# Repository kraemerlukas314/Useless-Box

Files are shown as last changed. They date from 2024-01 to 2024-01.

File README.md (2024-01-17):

# Useless-Box
Useless box project of Melvin Göttsche, Lukas Krämer and Mario Stötzel, Smart Technology Students at FH Wedel.  

This project was chosen as a freshmans project to learn about electronics, programming as well as basic manufacturing techniques such as laser cutting and 3d printing. More information about this project can be found in the [docs](https://github.com/kraemerlukas314/Useless-Box/tree/main/docs) folder of this repo (all in german).
If you want to build this project yourself, please check out the needed parts in the developer documentation.    
Image of our useless box

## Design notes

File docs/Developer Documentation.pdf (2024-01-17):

# Entwicklerdokumentation

# Useless Box mit Emotionen

## WS23/24, Smart Technology

## Melvin Göttsche, Lukas Krämer, Mario Stötzel

## Einführung

Als Erstsemesterprojekt haben wir uns dazu entschieden eine sogenannte Useless Box zu bauen. Diese besteht im Wesentlichen aus einem Schalter, der nach Umlegen durch den Nutzer mithilfe eines Servo Motors wieder in seine Ausgangsposition gebracht wird.

Die Useless Box ist zwar wenig sinnvoll, allerdings bietet sie sich insbesondere als erstes Projekt an, da sie
sowohl | elektronische | als | auch | mechanische | und | softwareseitige | Aspekte | beinhaltet.
Dieses Dokument soll einen guten Überblick über die Hardware sowie Software der Box vermitteln und dabei helfen, das Projekt gegebenenfalls nachzubauen, zu erweitern oder reparieren zu können.

## Überblick Hardware

Die Hardware der Useless-Box wurde auf Grundlage der verschiedenen Eigenschaften, die zu Beginn des Projektes für die Box ausgewählt wurden, festgelegt. Bei den Materialien haben wir uns für einfache Leimholzplatten entschieden. Diese Leimholzplatten haben eine Stärke von 4mm, was trotz des geringen Gewichtes die Stabilität, aber auch die Mobilität und Einfachheit der Useless-Box aufrechterhält. Die Box hat die Außenmaße von 22 x 12 x 12 cm (L/H/B), ist einfach zusammengesetzt und besteht aus einer Kiste mit einem zweigeteilten Deckel.

Wir haben eine besonders Eigenschaft hinzugefügt, mit der die Box mit Hilfe eines Displays Emotionen in Form von digitalen Gesichtern anzeigen kann. Um dieses umzusetzen, besitzt die eine Hälfte des Deckels der Useless-Box eine Vertiefung, die mit einer durchsichtigen Plexiglasscheibe abgedeckt wird, um das darunter befindlichen Displays zu schützen. Außerdem wurde auf dieser Seite der Box ein zusätzliches Loch ausgeschnitten, um einen Kippschalter für die Hauptfunktion der Box unterzubringen. Die andere Hälfte des Deckels ist einfach gestaltet und hat nur die Funktion einer Klappe.

In der Box selbst wurden für den Hauptmechanismus eine Halterung für einen Servo-Motor sowie mit der Grundplatte verleimte Standfüße zur Befestigung der Platine montiert.

Wesentliche Teile des Gehäuses, welche die Wände, den Boden, die Standfüße der Platine und Teile der Halterung für den Servo-Motor beinhalten, wurden als dauerhafte Verbindungen mit Leim befestigt. Andere Teile jedoch wie der Motor und die Platine wurden verschraubt, um eine Wartung zu ermöglichen. Die Plexiglasabdeckung wurde mit Silikon befestigt, um die Anzeige des Displays nicht zu beeinträchtigen. Die Klappe im Deckel wurde mit Scharnieren montiert.

Der Arm des Servo-Motors der Useless-Box ist das einzige Teil, welches aus Plastik in einem 3D-Drucker hergestellt wurde. Die Holzelemente und Plexiglaselemente wurden gelasert und nur einzelne Teile zusätzlich gebohrt. Alle Holzkomponenten wurden außerdem grundiert, geschliffen und dann in schwarz lackiert.

Zur Vorbereitung der Projektumsetzung haben wir zudem mit Hilfe einer Software und in Pappe ein 3D Model des Grundprinzips der Box entworfen, an welchem später noch Optimierungen bis zum finalen Produkt gefunden werden konnten.

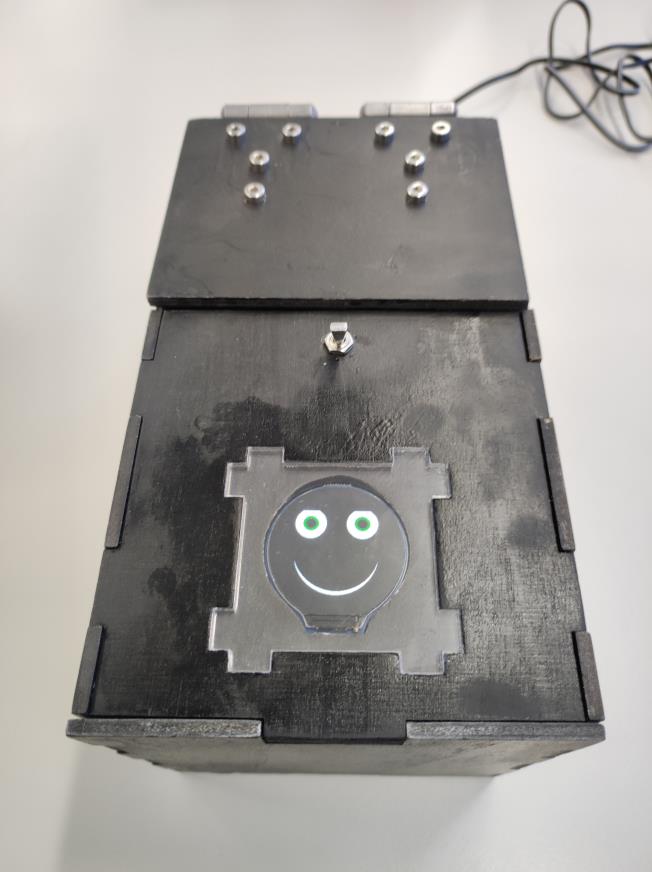
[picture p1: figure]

Bild 1: fertige Box

## Überblick Elektronik

Die Elektronik unserer Useless Box sollte in der Lage sein, einen Servo anzusteuern (für das Umlegen des Arms), einen Schalter auszulesen und dem Benutzer in Form eines Displays Feedback geben zu können. Angeboten hat sich daher die Nutzung eines Arduino Nano Mikrocontrollers, da er nicht nur unsere Anforderungen erfüllt, sondern wir durch private Projekte auch schon Erfahrung mit dem Board gesammelt haben und so die Entwicklung beschleunigt werden konnte.

Neben einem gewöhnlichen Schalter zum Umlegen, verwenden wir noch einen HiTec Servo, der den Arm bewegt, um später den Schalter umlegen zu können. Außerdem haben wir uns für ein rundes Display entschieden, was sich für das Darstellen von einem digitalen Gesicht als günstig erwies. Damit die Elektronik zuverlässig funktioniert und die Entwicklung nicht durch schwer reproduzierbare Wackelkontakte erschwert wird, haben wir uns von Anfang an dazu entschieden, für die gesamte Elektronik eine Leiterplatte zu erstellen.

Diese wurde zunächst in EasyEDA (Bild 2 und 3) designt und anschließend gefräst (Bild 4). Nach der Bestückung und kurzem Rauchtest haben wir nacheinander die Komponenten eingebaut und die Subsysteme der Reihe nach getestet.

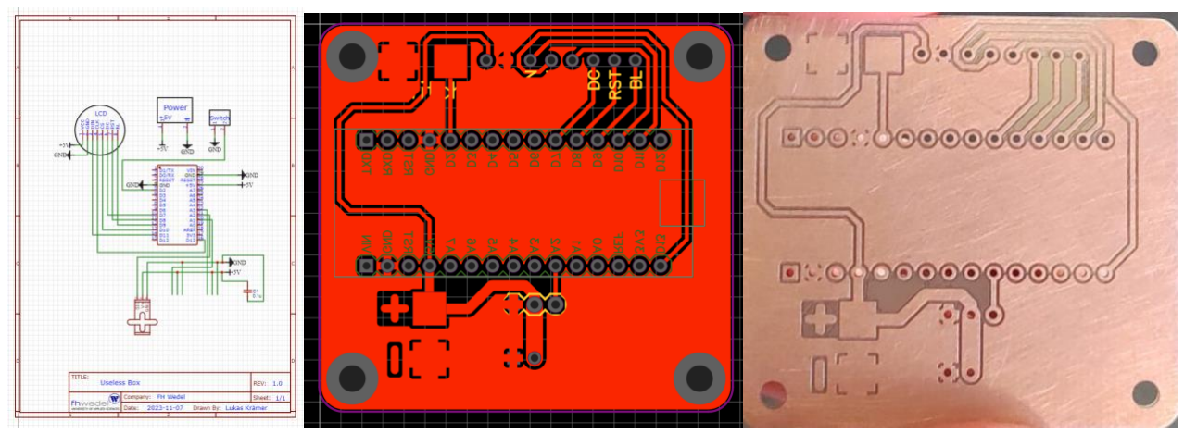
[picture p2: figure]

Bild 2: Schaltplan | Bild 3: Platine | Bild 4: gefräste Platine

## Überblick Software

Die Box fängt damit an den Zähler auf dem Display anzuzeigen, wie oft der Schalter bereits umgelegt worden ist. Sie zeigt diese Zahl so lange an, bis der Schalter umgelegt wird. Hiernach wird der Arm ausgefahren, bis der Schalter umgelegt wurde. Dies wird genutzt, um die Position des Schalters intern zu speichern. Damit sich die Box “merken” kann, wie oft der Schalter bereits umgelegt wurde, schreiben wir einen Zähler (unsigned, vier bytes groß) nach jedem Umlegen in die EEPROM des Arduinos. Da eine einzelne EEPROM Speicherzellen lediglich 100.000-mal beschrieben werden kann (100.000 stehen als “garantiert” im Datenblatt, unabhängige Tests ergaben deutlich höhere Zahlen) und wir dafür sorgen möchten, dass unsere Box auch so lange wie möglich korrekt funktioniert, haben wir uns dazu entschieden, ein rollierendes System zu verwenden, was im Folgenden näher erläutert wird. Das Abspeichern in die EEPROM erfolgt byteweise, also könnte man in Adresse 0 das LSB schreiben und die anderen drei Bytes in Adressen 1, 2 und 3. Da das aber nach 100.000 Schreibzyklen nicht mehr garantiert funktionieren würde, werden Byte 1, 2 und 3 in die Adressen 16, 17 und 18 geschrieben. Das LSB, was sich am häufigsten ändert, wird hingegen in einer Adresse zwischen 0 und 15 abgespeichert. Wird der Code initial auf dem Arduino ausgeführt, befindet sich in den Adressen 0 bis 15 überall eine 0, der Arduino wählt nun per “Zufallsgenerator” (millis mod 16) eine der Adressen aus und schreibt dort eine
1. Beim nächsten Schalterumlegen sucht er jetzt in den Adressen zwischen 0 und 15 die Adresse, deren Wert größer als 0 ist, folglich wird wieder in dieselbe Adresse wie zuvor geschrieben, bis der Wert 256 bzw. 0 erreicht wird. Dort wird dann erneut eine zufällige Adresse ausgewählt, um das LSB des Zählers abzuspeichern, die sich sehr wahrscheinlich (93,75%) von der letzten Adresse unterscheidet. Dadurch verschleißt die EEPROM deutlich langsamer und kann zumindest Zähler bis 1,6 Millionen garantiert abspeichern. Natürlich kann dieses System beliebig erweitert werden, sodass beispielsweise die ersten 32 oder 64 Adressen fürs Rollieren genutzt werden, was die Langlebigkeit weiter steigern würde.

Die Hauptmethode der Useless Box ist der Loop des Arduinos. Dieser wurde mit einer while Schleife getaktet, um die Animationen besser vorherzusehen. Sollte der Schalter in der Off-Position stehen, wird eine Variable happiness bis zu einem bestimmten Wert erhöht. Sollte der Schalter umgelegt worden sein und es läuft noch keine Animation, wird eine Animation zufällig ausgewählt, der Zähler für die Gesamtzahl der Schalterumlege erhöht und die happiness um einen Wert reduziert. Sollte der Schalter vom Nutzer wieder zurückgelegt worden sein, während eine Animation noch läuft, so wird die Animation abgebrochen und der Arm zurückgefahren. Sollte eine Animation noch laufen, so wird eine Funktion aufgerufen, die wiederum die Funktion für die Animation direkt aufruft. Die Animationen werden in Steps aufgeteilt, damit die Main “zeitgleich” nebenbei laufen kann. Der erste Step jeder Animation ist es, den Servo zu attachen. In jedem Step wird, nachdem der Step abgeschlossen ist ein Zähler erhöht, welcher repräsentiert, welcher Step gerade dran ist. Um den Arm zu bewegen kann eine Funktion verwendet werden, der man sagen kann, wo der Arm hinsoll und in wie vielen Schritten er dort ankommen soll. Hierfür bestimmt die Funktion beim ersten Aufruf wie weit sich der Arm bei jedem Aufruf bewegen soll und gibt true zurück, wenn die finale Position erreicht worden ist.

Sollte im Moment keine Animation aktiv sein, wird das Gesicht auf dem Display aktualisiert. Hierbei wird die Variable happiness betrachtet und das Gesicht wird dementsprechend glücklich oder unglücklich gezeichnet. Bei jedem x-ten Aufruf der Hauptfunktion wird außerdem eine Funktion aufgerufen, die die Box blinzeln lässt, um sie humaner rüberkommen zu lassen.

## Was wir nächstes Mal besser machen würden

Für unser nächstes Projekt sollten wir von Anfang an den Aspekt der einfachen Wart- und Reparierbarkeit denken, da bei uns aktuell viele Teile dauerhaft fest geleimt oder nur schwer erreichbar sind. Mit genug Zeit lässt sich zwar jedes Teil tauschen, allerdings ist dies teils mit hohem Aufwand verbunden.

## Wartungstätigkeiten

Zwar ist es schwierig, nach lediglich so kurzer Nutzung potentielle “Point of Failures” aufzuführen, wahrscheinlich wird jedoch als Erstes unser einziges bewegliches Teil, der Servo, versagen. Dieser kann getauscht werden, indem man zunächst die “Serviceklappe” hochhebt, die Servohalterung abschraubt und anschließend den Servo selbst aus seiner Halterung entfernt. Nach Einsetzen des neuen Servos, sollte die finale Servoposition anhand der beiden großen Schrauben, welche die Servohalterung mit der Box verbinden adjustiert werden, damit die Hand den Schalter der Box korrekt umlegen kann.

## Weiterentwicklung

Was die Weiterentwicklung des Projektes betrifft, haben wir über das Ergänzen von RGB Leds nachgedacht, die zusätzlich zum Display die Emotionen der Box darstellen können. Diese könnte entweder von außen an die Box angebracht werden oder aber in Form von RGB-Streifen von innen in die Box geklebt werden, sodass sie durch die Klappe der Box scheinen, sobald der Servo diese hochhebt. Außerdem könnte eine SD-Karte mit verschiedenen Soundeffekten samt kleinem Lautsprecher ergänzt werden, um die Nutzung der Box noch interessanter zu gestalten. Abgespielt werden können dabei zum Beispiel Soundeffekte beim Umlegen des Schalters (bspw.: stöhnen, wenn die Box genervt ist). Zu guter Letzt können die von uns erstellen Animationen softwareseitig natürlich beliebig erweitert oder abgeändert werden, was die Nutzung der Box sicherlich interessanter machen würde. Die Weiterentwicklung des Codes darf natürlich gerne in Form einer Pull-Request in unser Repository ergänzt werden.

## Einrichten der Entwicklungsumgebung

Um an der Box weiterarbeiten zu können, muss zunächst die Arduino IDE (https://www.arduino.cc/en/software) heruntergeladen und installiert werden. Außerdem werden noch die beiden Libraries “Adafruit_GFX” (https://github.com/adafruit/Adafruit-GFX-Library) und “Adafruit_GC9A01A” (https://github.com/adafruit/Adafruit_GC9A01A) benötigt. Damit das Abspeichern des Schalterzählers in die EEPROM wie erwartet funktioniert, sollten außerdem die ersten 19 Adressen (also 0 bis 18) mit einer 0 beschrieben werden, dies erfolgt über den Befehl EEPROM.write(Adresse, 0). (https://docs.arduino.cc/learn/built-in-libraries/eeprom)

Der gesamter Sourcecode samt weiter Informationen ist in unserem GitHub Repository (https://github.com/kraemerlukas314/Useless-Box/) zu finden.

## Teileliste

- Arduino Nano (https://store.arduino.cc/products/arduino-nano)
- Waveshare 1.28inch Round LCD Module Display (https://www.amazon.de/dp/B08V5538C6)
- Servo HS-645MG (https://www.servonaut.de/shop/en/product_info.php?info=p460_servo-hs-645mg.html)
- 5V Netzteil (2.5A) (https://www.conrad.de/de/p/voltcraft-vc-11332635-steckernetzteil-festspannung-5-v-dc-2-5-a-12-5-w-2266527.html)
- Buchse zum Netzteil (https://www.conrad.de/de/p/tru-components-niedervolt-steckverbinder-buchse-einbau-vertikal-5-5-mm-2-5-mm-1-st-1564887.html)
- Schalter (https://www.conrad.de/de/p/tru-components-1587776-tc-ta101f1-kippschalter-250-v-ac-3-a-1-x-aus-ein-rastend-1-st-1587776.html)
- 2x Scharnier 35mm*125mm*1,5mm mit M4 Löchern
- 100 µF Elektrolyt-Kondensator (https://www.conrad.de/de/p/teapo-sy-100-f-16v-6-3-x11mm-elektrolyt-kondensator-radial-bedrahtet-2-5-mm-100-f-16-v-20-o-x-l-6-3-mm-x-11-mm-1-443906.html)
- 8x Senkkopfschraube M4 10mm (https://www.conrad.de/de/p/toolcraft-888802-senkkopfschrauben-m3-20-mm-t-profil-mit-stift-edelstahl-a2-10-st-888802.html)
- 8x Schraube M4 14mm
- 16x Mutter M4
- 8x Schraube M3 10mm
- 8x Mutter M3
- 2x Unterlegscheibe M5
- 2x Unterlegscheibe M6
- 2x Schraube M5 45mm
- 1420cm²
Leimholzplatten, 4mm dick (ohne Bohrungen)
- Holzblock 72 cm²
- 1m 0.75mm² Kupferkabel
- Holzleim
- Spraydose Grundierung
- Spraydose Scharz (Matt)
- 28cm² Plexiglas
- Silikon
- 2x Schraubenniete M5

## Werkzeug

- Mini USB Kabel, zum Hochladen von Code auf den Arduino
- Lötkolben
- Lötzinn
- Abisolierzange
- Entsprechende Schraubendreher
- Schraubzwingen, um geleimte Teile zu fixieren
- Lasercutter
- 3D Drucker
- Kartuschenpresse
- Schleifpapier
- Feilen
- Nietenzange

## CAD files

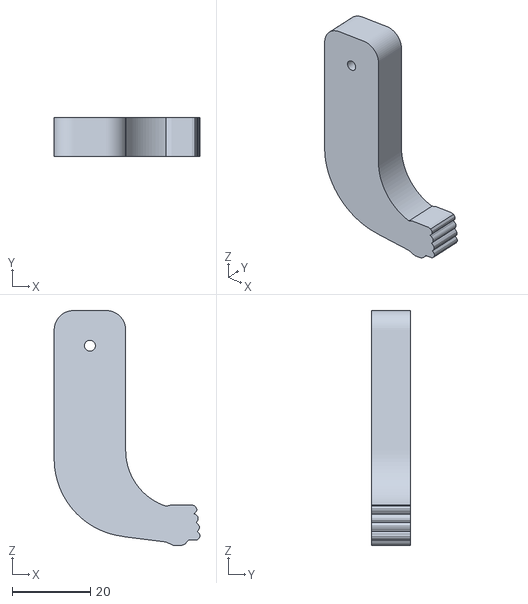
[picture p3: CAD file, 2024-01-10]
files/Hardware/arm.stl
37.3 x 10.0 x 60.2

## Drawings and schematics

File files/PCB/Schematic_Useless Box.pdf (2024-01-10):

## LCD

+5V -

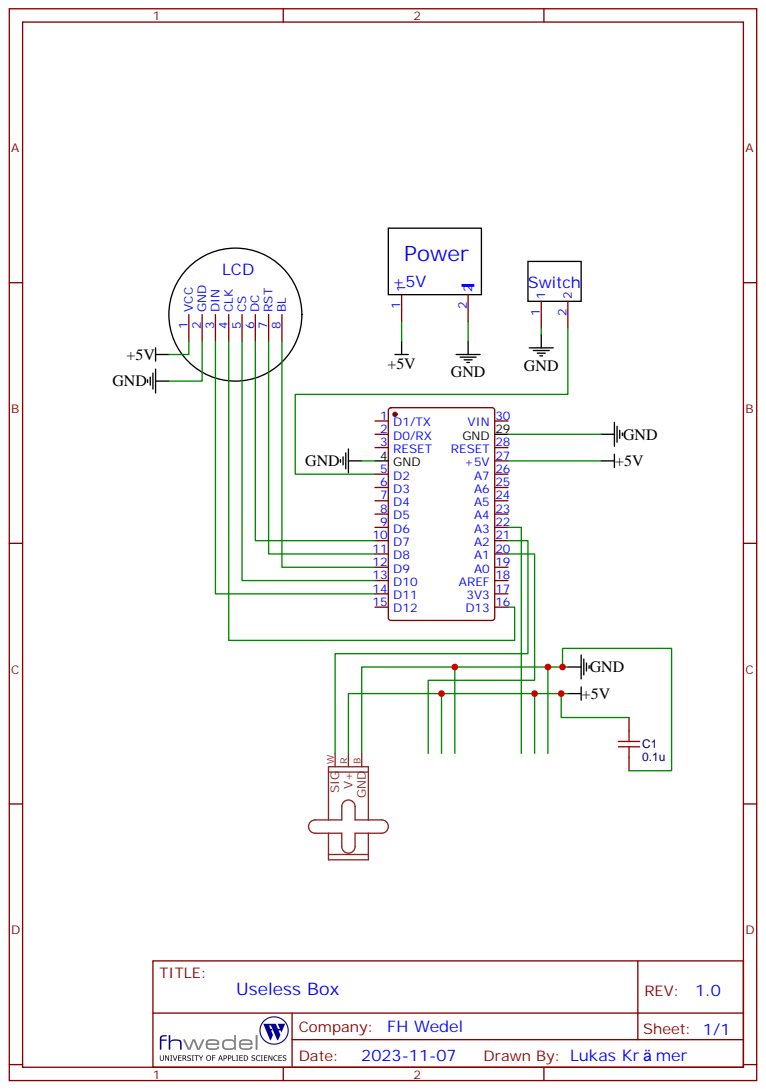
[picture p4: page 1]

Drawn By: Lukas Kr mer

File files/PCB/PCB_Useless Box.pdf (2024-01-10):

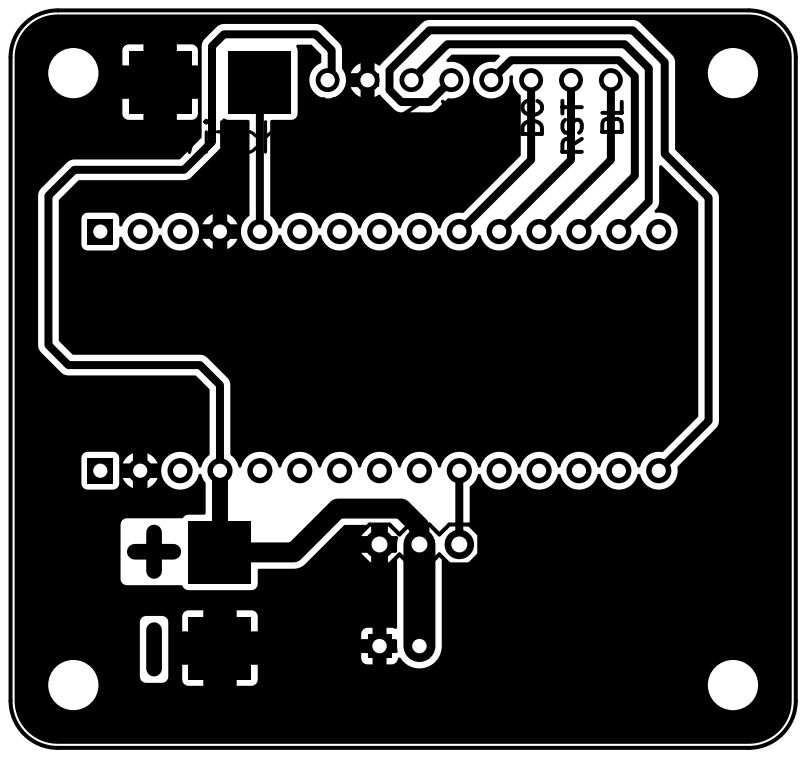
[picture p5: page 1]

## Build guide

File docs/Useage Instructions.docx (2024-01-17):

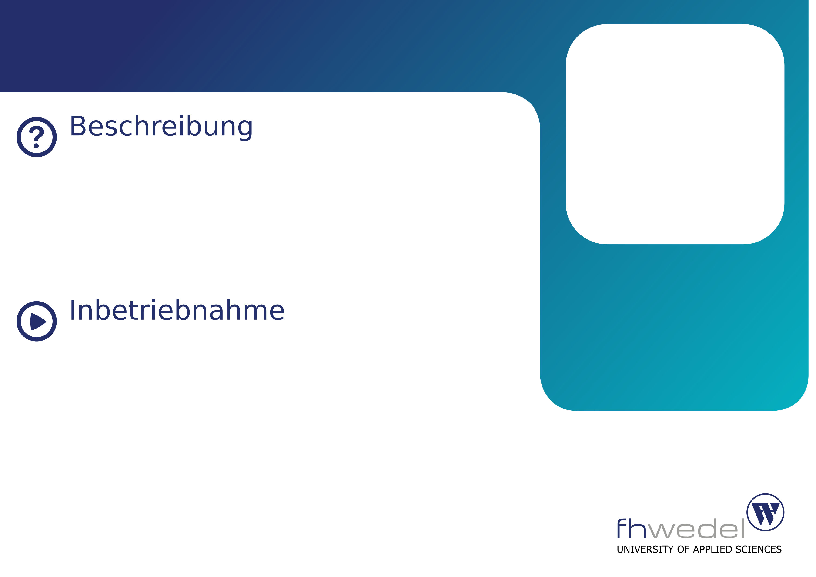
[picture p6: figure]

Useless Box

Diese Useless Box ist als Erstsemesterprojekt entstanden, dessen Ziel es war, möglichst viele Maschinen zu nutzen, um die Box zu fertigen und Erfahrung für den späteren Studienverlauf zu sammeln. So kamen unter anderem ein Laser Cutter (Gehäuse), ein 3D Drucker (Arm) und eine Fräse (Platine) zum Einsatz.

1. Semester | WS23

Lukas Krämer

Mario Stötzel

Melvin Finn Göttsche

Zum Einschalten der Box muss lediglich das Netzteil eingesteckt werden. Anschließend kann der Schalter „nach oben“ umgelegt werden, der dann automatisch zurück in die Ausgangsposition gebracht wird.

Nach dem Umlegen des Schalters sollte stets darauf gewartet werden, dass er von der Maschine zurückgelegt wird, also bitte nicht manuell den Schalter fünf mal hin und her schalten.

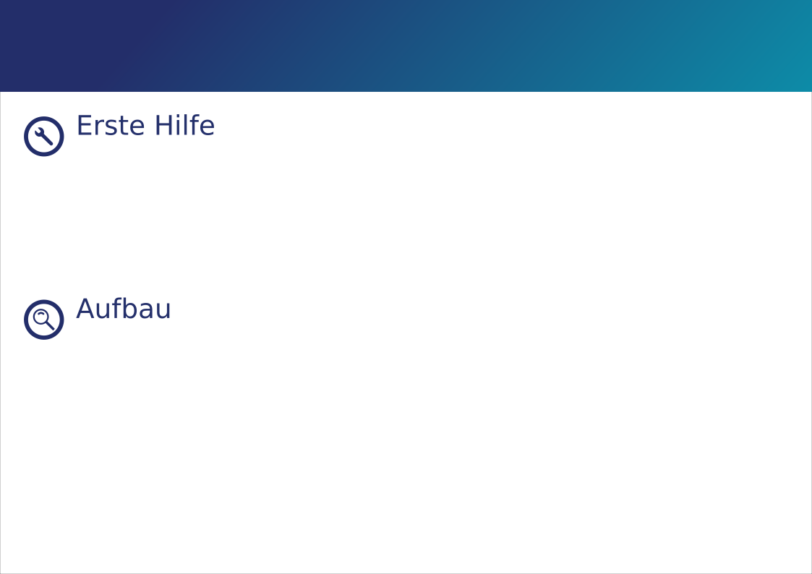
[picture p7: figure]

Die Überschrift

Q: Die Box ignoriert mich

A: Bitte lege den Schalter um

In allen anderen Fällen: „Have you tried turning it off and on again?“

Falls auch das nicht hilft, ist vermutlich ein Kabel im Inneren der Box abgerissen. Bitte wende dich an ein Mitglied der FH Wedel.

Das Herzstück unserer Useless Box bildet ein Mikrocontroller, an den ein Servomotor, das zu sehende Display sowie der Schalter angeschlossen sind.

Sobald der Schalter umgelegt wird, steuert der Mikrocontroller den Servomotor an, um ihn wieder in seinen Ausgangszustand zu bewegen. Außerdem wird darauf basierend die Emotionslage angepasst.

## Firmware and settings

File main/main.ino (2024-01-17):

#include "defines.h"

Adafruit_GC9A01A tft(TFT_CS, TFT_DC);

Servo servo;

int eyesColor = 0x0066ff;
int eyesColorSize = EYES_SIZE / 2;
int eyesPupilSize = EYES_SIZE / 2.8;
long timeLast = millis();
int happiness = random(100);
int blinker = 0;
int blinkTimer = 200;
byte servoPosSwitch = 0;
byte servoPosHome = 0;
byte servoPosCurrent = 0;
byte SERVO_TOGGLE_POS; // is a variable but is only changed once
byte SERVO_HOME_POS;
const byte SERVO_DELTA_TOOGLE_HOME = 120; // difference between toogle pos and home pos
int activeAnimation = -1;
int eyeLeftActualPositionX = 0;
int eyeLeftActualPositionY = 0;
int eyeRightActualPositionX = 0;
int eyeRightActualPositionY = 0;
int eyeLidActualPositionLL = 0;
int eyeLidActualPositionLR = 0;
int eyeLidActualPositionRL = 0;
int eyeLidActualPositionRR = 0;
int mouthActualStatus = -100000;
int eyesActualColor = 0;
bool buttonPushedByArm = true;
int animationStep = 0;
bool animationFinished = true;
bool armAnimationInited = false;
int armAnimationDeg = 0;
bool sleeping = false;
int tiredness = 0;
int sleepTimer = 200;
int maxSleepZs = 3;
int sleepZCounter = maxSleepZs;

void setup()
{
  randomSeed(analogRead(0));
  Serial.begin(115200);
  Serial.println("---- NEW START ----");
  tft.begin();
  pinMode(PIN_BTN, INPUT_PULLUP);
  servo.attach(PIN_SERVO);
  servo.write(180);
  servo.detach();
  displayClear();

  // if counter is < 999999 -> fill empty digits with zeros so string always has length 6
  String formattedString = String(getButtonPresses());
  while (formattedString.length() < 6)
  {
    formattedString = "0" + formattedString;
  }
  tft.setTextSize(6);
  tft.setCursor(16, 95);
  tft.print(formattedString);

  // wait for user to toggle button
  while (!getButtonState())
  {
  }
  servo.attach(PIN_SERVO);
  // Calibrate servo position
  servoPosCurrent = servo.read();
  while (getButtonState() && servoPosCurrent > 0)
  {
    servoPosCurrent = servoPosCurrent - 1;
    servo.write(servoPosCurrent);
    delay(15);
  }
  SERVO_TOGGLE_POS = servoPosCurrent + 7;
  SERVO_HOME_POS = 180; // SERVO_TOGGLE_POS + SERVO_DELTA_TOOGLE_HOME;
  servo.write(SERVO_HOME_POS);
  Serial.println("SERVO_HOME_POS: " + String(SERVO_HOME_POS));
  Serial.println("SERVO_TOGGLE_POS: " + String(SERVO_TOGGLE_POS));
  displayClear();
  eyesRedraw();
  eyeLidsRedraw();
  mouthDrawStatus(0);
  servo.detach();
}

void loop()
{
  while (millis() - timeLast < intervall)
  {
  }
  timeLast = millis();

  if (!getButtonState() && activeAnimation == -1)
  {
    if (happiness < MAX_HAPPINESS)
    {
      happiness += happinessAdder;
    }

    if (tiredness < SLEEP_TIME)
    {
      tiredness++;
    }
    if (!sleeping)
    {
      handleStandardExpression();
    }
  }
  else if (!getButtonState() && activeAnimation != -1 && !buttonPushedByArm)
  {
    Serial.println("Button pressed while playing animation. Cancelling animation...");
    armAnimationInited = false;
    resetAnimation();
    activeAnimation = -1;
    animationStep = 0;
    if (happiness + happinessAdder * 10 <= MAX_HAPPINESS)
    {
      happiness += happinessAdder * 10;
    }
  }
  else if (getButtonState() && activeAnimation == -1)
  {
    if (happiness - dissatisfaction >= MIN_HAPPINESS)
    {
      happiness -= dissatisfaction;
    }
    activeAnimation = random(1, maxArmAnimations + 1);
    animationStep = 0;
    buttonPushedByArm = false;
    incrementButtonPresses();
    if (tiredness - 3000 > 0)
    {
      tiredness -= 3000;
    }
    else
    {
      tiredness = 0;
    }
    sleeping = false;

    Serial.println("Starting new animation: " + String(activeAnimation));
  }

  if (activeAnimation != -1)
  {
    handleStandardExpression();
    handleButtonPressed();
    blinker = blinker / 2;
  }

  // Blinking
  if (blinker <= 0 && !sleeping)
  {
    eyesBlink();
    blinker = blinkTimer;
  }
  else
  {
    --blinker;
  }
  if (sleeping)
  {

    if (sleepTimer <= 0)
    {
      if (sleepZCounter >= maxSleepZs)
      {
        displayClear();
        sleepZCounter = 0;
      }
      tft.setTextSize(random(3, 7));
      tft.setCursor(random(25, 215), random(25, 215));
      tft.print('z');
      sleepZCounter++;
      sleepTimer = 200;
    }
    else
    {
      sleepTimer--;
    }
  }
}

bool getButtonState()
{
  static int lastButtonState = HIGH, buttonState;
  static unsigned long lastDebounceTime;

  buttonState = digitalRead(PIN_BTN);
  if (buttonState != lastButtonState)
    lastDebounceTime = millis();

  return !((millis() - lastDebounceTime) > 50 ? lastButtonState = buttonState : !lastButtonState);
}

// increments the total button counter and writes result to EEPROM
void incrementButtonPresses()
{
  EEPROMWritelong(getButtonPresses() + 1);
}

uint32_t getButtonPresses()
{
  // TODO: read from eeprom:
  byte one = 0;
  for (int i = 0; i < 16; ++i)
  {
    if (EEPROM.read(i) > 0)
      one = EEPROM.read(i);
  }
  byte two = EEPROM.read(16);
  byte three = EEPROM.read(17);
  byte four = EEPROM.read(18);
  return (uint32_t)four << 24 | (uint32_t)three << 16 | (uint32_t)two << 8 | (uint32_t)one;
}

void EEPROMWritelong(long value)
{
  byte one = (value & 0xFF);
  byte two = ((value >> 8) & 0xFF);
  byte three = ((value >> 16) & 0xFF);
  byte four = ((value >> 24) & 0xFF);

  // to avoid eeprom wear down, least significant byte (that changes very frequently)
  // is written somewhere between address 0 and 15
  byte address_to_write = 0;
  for (int i = 0; i < 16; ++i)
  {
    if (EEPROM.read(i) > 0)
      address_to_write = i;
  }
  // there's 0 in every address, so choose random between 0 and 15
  if (address_to_write == 0)
  {
    address_to_write = millis() % 16;
  }
  EEPROM.write(address_to_write, one);
  EEPROM.write(16, two);
  EEPROM.write(17, three);
  EEPROM.write(18, four);
}

void displayClear()
{
  // Clear Display (Set display to background color)
  tft.fillScreen(BACKGROUND);
}

/*********************************************************************************************************
  END FILE
*********************************************************************************************************/

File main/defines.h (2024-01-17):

// include libraries
#include "Adafruit_GFX.h"
#include "Adafruit_GC9A01A.h"
#include <EEPROM.h>
#include <Servo.h>

// pin defines
#define PIN_BTN 2
#define PIN_SERVO A2

#define TFT_DC 7
#define TFT_CS 10

// display defines
#define WHITE 0xffffff
#define BLACK 0x000000
#define BACKGROUND BLACK
#define MOUTH_COLOR WHITE
#define X_MIN 0
#define Y_MIN 0
#define X_MAX 240
#define Y_MAX 240
#define Y_MOUTH_START Y_MAX / 2.2
#define MOUTH_THICKNESS 20
#define MOUTH_MID Y_MAX * 0.625
#define EYES_DISTANCE_EDGES 40
#define EYES_SIZE 30
#define EYE_LEFT_MIDDLE_X EYES_DISTANCE_EDGES + EYES_SIZE
#define EYE_LEFT_MIDDLE_Y EYES_DISTANCE_EDGES + EYES_SIZE
#define EYE_RIGHT_MIDDLE_X (X_MAX - (EYES_DISTANCE_EDGES + EYES_SIZE))
#define EYE_RIGHT_MIDDLE_Y EYES_DISTANCE_EDGES + EYES_SIZE
#define intervall 10
#define dissatisfaction 600
#define happinessAdder 1
#define MIN_HAPPINESS -1500
#define MAX_HAPPINESS 1000
#define SLEEP_TIME 5000
#define maxArmAnimations 5
#define MOUTH_POSITION_BOTTOM 30

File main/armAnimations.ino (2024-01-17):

#include "defines.h"

void resetAnimation()
{
    if (moveArm(SERVO_HOME_POS, 1))
    {
        armAnimationInited = false;
        activeAnimation = -1;
        animationStep = 0;
        animationFinished = true;
        servo.detach();
    }
}

void animation1()
{
    switch (animationStep)
    {
    case 0:
        Serial.println("AnimationStep: " + String(animationStep));
        servo.attach(PIN_SERVO);
        animationStep++;

        break;

    case 1:
        Serial.println("AnimationStep: " + String(animationStep));
        if (moveArm(SERVO_TOGGLE_POS, 5))
        {
            armAnimationInited = false;
            animationStep++;
        }
        break;

    case 2:
        Serial.println("AnimationStep: " + String(animationStep));
        if (moveArm(SERVO_HOME_POS, 2))
        {
            armAnimationInited = false;
            animationStep++;
        }
        break;
    case 3:
        Serial.println("AnimationStep: " + String(animationStep));
        servo.detach();
        animationFinished = true;
        animationStep = 0;
        activeAnimation = -1;
        break;

    default:
        break;
    }
}

void animation2()
{
    switch (animationStep)
    {
    case 0:
        servo.attach(PIN_SERVO);
        animationStep++;
        break;

    case 1:
        if (moveArm(SERVO_HOME_POS - ((SERVO_HOME_POS - SERVO_TOGGLE_POS) / 2), 2))
        {
            armAnimationInited = false;
            animationStep++;
        }
        break;

    case 2:
        if (moveArm(SERVO_HOME_POS, 1))
        {
            armAnimationInited = false;
            animationStep++;
        }
        break;

    case 3:
        delay(random(500, 1500));
        armAnimationInited = false;
        animationStep++;
        break;

    case 4:
        if (moveArm(SERVO_TOGGLE_POS, 1))
        {
            armAnimationInited = false;
            animationStep++;
        }
        break;

    case 5:
        delay(1000);
        armAnimationInited = false;
        animationStep++;
        break;

    case 6:
        if (moveArm(SERVO_HOME_POS, 1))
        {
            armAnimationInited = false;
            animationStep++;
        }
        break;

    case 7:
        servo.detach();
        animationFinished = true;
        animationStep = 0;
        activeAnimation = -1;
        break;

    default:
        break;
    }
}

void animation3()
{
    switch (animationStep)
    {
    case 0:
        servo.attach(PIN_SERVO);
        animationStep++;
        break;

    case 1:
        delay(random(0, 2000));
        armAnimationInited = false;
        animationStep++;
        delay(random(0, 1000));
        break;

    case 2:

        if (moveArm(SERVO_TOGGLE_POS + 10, 1))
        {
            armAnimationInited = false;
            animationStep++;
        }
        break;

    case 3:
        if (moveArm(SERVO_HOME_POS, 1))
        {
            armAnimationInited = false;
            animationStep++;
        }
        break;

    case 4:
        delay(random(300, 1500));
        armAnimationInited = false;
        animationStep++;
        break;

    case 5:
        if (moveArm(SERVO_TOGGLE_POS, 1))
        {
            armAnimationInited = false;
            animationStep++;
        }
        break;

    case 6:
        if (moveArm(SERVO_HOME_POS, 1))
        {
            armAnimationInited = false;
            animationStep++;
        }
        break;

    case 7:
        servo.detach();
        animationFinished = true;
        animationStep = 0;
        activeAnimation = -1;
        break;

    default:
        break;
    }
}

void animation4()
{
    switch (animationStep)
    {
    case 0:
        servo.attach(PIN_SERVO);
        animationStep++;
        break;

    case 1:
        for (byte i = 0; i < random(1, 40); i++)
        {
            moveArm(SERVO_HOME_POS - 10, 1);
            delay(300);
            moveArm(SERVO_HOME_POS, 1);
        }
        armAnimationInited = false;
        animationStep++;
        break;

    case 2:
        for (byte i = 0; i < random(1, 5); i++)
        {
            moveArm(SERVO_TOGGLE_POS + 3, 1);
            delay(random(200, 500));
            moveArm(SERVO_HOME_POS - ((SERVO_HOME_POS - SERVO_TOGGLE_POS) / 2), 1);
        }
        armAnimationInited = false;
        animationStep++;
        break;

    case 3:
        if (moveArm(SERVO_HOME_POS, 3))
        {
            armAnimationInited = false;
            animationStep++;
        }
        break;

    case 4:
        servo.detach();
        animationFinished = true;
        animationStep = 0;
        activeAnimation = -1;
        break;

    default:
        break;
    }
}

void animation5()
{
    switch (animationStep)
    {
    case 0:
        servo.attach(PIN_SERVO);
        animationStep++;
        break;

    case 1:
        if (moveArm(SERVO_TOGGLE_POS, 20))
        {
            armAnimationInited = false;
            animationStep++;
        }
        break;
    case 2:
        if (moveArm(SERVO_TOGGLE_POS + 10, 2))
        {
            armAnimationInited = false;
            animationStep++;
        }
        break;

    case 3:
        if (moveArm(SERVO_TOGGLE_POS - 10, 1))
        {
            armAnimationInited = false;
            animationStep++;
        }
        break;

    case 4:
        delay(random(500, 3000));
        armAnimationInited = false;
        animationStep++;
        break;

    case 5:
        if (moveArm(SERVO_HOME_POS, 5))
        {
            armAnimationInited = false;
            animationStep++;
        }
        break;

    case 6:
        servo.detach();
        animationFinished = true;
        animationStep = 0;
        activeAnimation = -1;
        break;

    default:
        break;
    }
}

void animation6()
{
    switch (animationStep)
    {
    case 0:
        servo.attach(PIN_SERVO);
        animationStep++;
        break;

    case 1:

        break;

    default:
        break;
    }
}
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

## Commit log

2023-11-01 rgb led test, untested
2023-11-22 save button presses to eeprom
2023-11-29 Ladescreen after power up
2023-12-06 centered button counter
2023-12-06 servo calibration
2023-12-13 proper servo calibration using constants
2023-12-13 not working eeprom code
    [Display.ino]
2023-12-13 mouth, eyes flash fixed
    [Display.ino, eyes.ino, mouth.ino]
2023-12-20 arm animation fixed
2024-01-03 edited Function buttonPressed to handleButtonPressed
2024-01-10 added docs and updated README
    [arm.stl]
